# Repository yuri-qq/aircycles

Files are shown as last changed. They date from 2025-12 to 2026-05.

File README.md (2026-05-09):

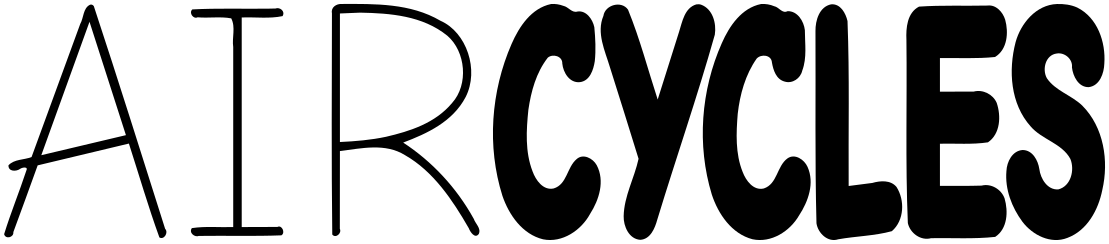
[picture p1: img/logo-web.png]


# Air Cycles

Air Cycles is our budget air purifier design for 39C3 (slogan "Power Cycles").

It is a [Corsi-Rosenthal box][cr] heavily inspired by the "Luggable" design by [cleanairkits][] (5 fans version).

<table><tr>
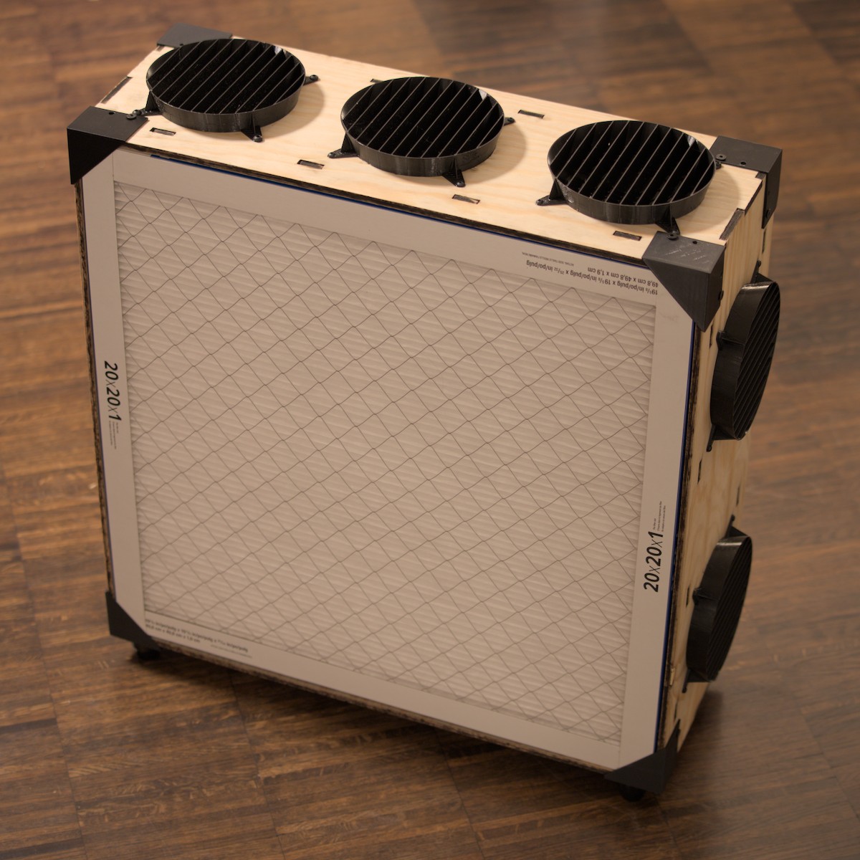
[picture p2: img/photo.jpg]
Photo of a fully assembled unit
   <td></td>
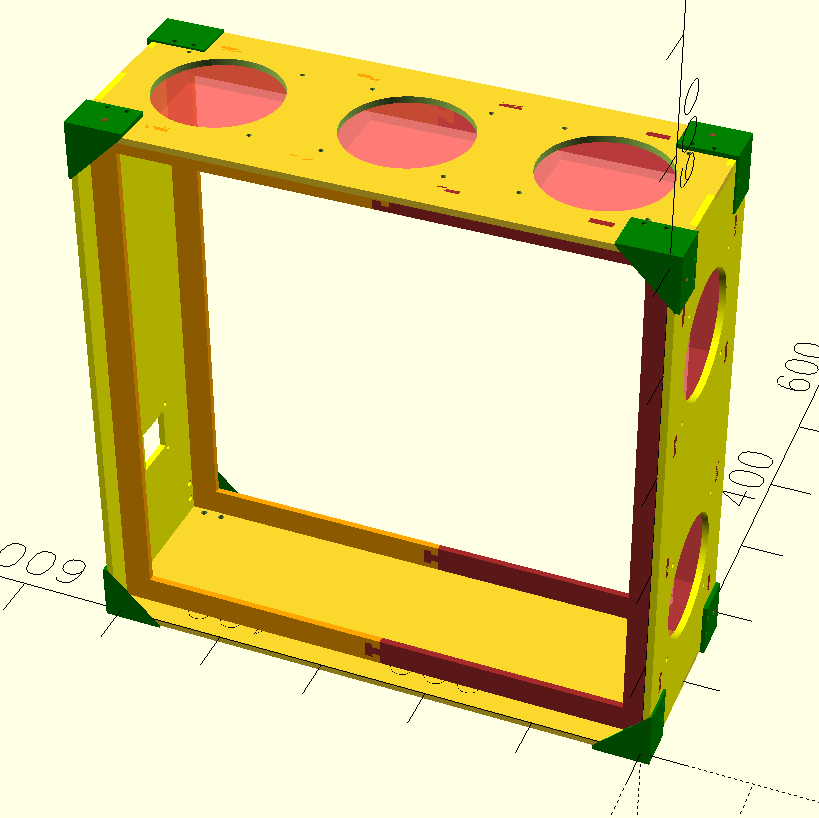
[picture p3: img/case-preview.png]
Preview 3D render in openscad
   <td></td>
</tr></table>

[cr]: https://en.wikipedia.org/wiki/Corsi%E2%80%93Rosenthal_Box
[cleanairkits]: https://www.cleanairkits.com

## Goals

* Filter airborne viruses from the air
* Use filters with the least air resistance
* Quiet enough to not be a nuisance
* Reasonably cheap
* Easy to assemble and disassemble
* Compact for storage
* Parametric design, adaptable to any filter size
* Look moderately professional

## Why?

We're the infektionsschutz team of 39C3. We take care of buying and distributing masks and tests.

This year we tried and failed to get some budget (money and storage) allocated for air purifiers. So we decided to make our own with a focus on being able to store them ourselves between events.

Also, for fun, to learn to work with wood, to use the laser cutter at the local makerspace.

## Is it any good?

For air filtering, we expect it to perform at least as well as the cleanairkits [Luggables "5 SickleFlow DIY KIT"](https://www.cleanairkits.com/en-eu/products/luggables-europe?variant=51819663655212). Their website has plenty of information about efficiency.

We don't have any budget to do real testing ourselves, but we can do a rough estimation of Dust/Virus CADR by multiplying the sum of CFM of all fans by 0.7. This ignores several variables, like pressure specs of the fans and size of the filters, but hopefully errs on the conservative side.

| Cleanairkits designs | Raw CFM | Dust CADR (measured)  |
| --- | --- | --- |
| 5 Sickleflow (16x25x1") | 310 | 218 |
| 7 Sickleflow (20x25x1") | 434 | 323 |
| 7 Mobius 120p (20x25x1") | 526 | 401 |

All our variants use 20x20x1" filters, equivalent to the 16x25x1" ones. Almost all of them have 5 fans, but except the last one in this list which has 6 as an experiment.

| Variants we've used in v1 | Raw CFM | Dust CADR (estimated) |
| --- | --- | --- |
| 5 Mobius 120 | 316 | 221 |
| 5 Mobius 120 OC | 441 | 308 |
| 3 Mobius, 2 Mobius OC | 366 | 256 |
| 2 Mobius, 2 Mobius OC, 1 Sunon | 441 | 309 |
| 2 Mobius, 3 Mobius OC, 1 Sunon | 530 | 371 |

In the current iteration, it is not necessarily cheaper or easier to build. Our project is more focused on ease of disassembly, reassembly, and storage.

## Decisions made for v1 (2025, 39c3)

Feel free to contact us with opinions or criticism!

### Overall shape

Two filters on a wooden frame with 5 fans on the sides pulling air inwards.

The traditional corsi-rosenthal cube takes up too much floor space, and box fans are not widely available in europe.

### Filters

Two 3M Filtrete MERV 13 / MPR 1900 filters, 20x20x1 inch.

They are the most common choice for Corsi-Rosenthal boxes and we had 10 of these in storage from previous years.

The 20x20x1 inch variant has the same surface as the 16x25x1 inch filters used by cleanairkits in their 5 fan Luggable model.

These filters are typically easily acquirable in europe through digikey, although the 20x20x1 inch variant has been out of stock for a few months.

**Next year:** we'll evaluate european sources for filters, likely F7 ePM1.

### Fans

A mix of five of these 120mm fans:

* Coolermaster Mobius 120
* Coolermaster Mobius 120 OC
* Sunon EEC0381B1-000U-A99

Typically three Mobius 120 OC and two Mobius 120.

Primarily inspired by cleanairkits, these fans have a great balance of static pressure specs and noise levels.

The Mobius 120 OC variant is slighly noisier but has significantly better static pressure, and happened to be cheaper at times.

In some cases where noise is more tolerated, we added some Sunon fans (EEC0381B1-000U-A99) to the mix, which have excellent static pressure specs, better airflow, more professional datasheets, but are completely uninterested in being quiet.

**Considered but rejected:** Everyone loves Noctua but most of their fans focus on airflow, not static pressure, so they are not suitable for putting a filter in front of them. Only their newest model, "NF-A12x25 G2 PWM", has slightly better pressure than the Mobius 120 at the same noise level and airflow, but for three times the price.

**Next year:** possibly more Sunon fans in the mix, as we found some locations are very tolerant of noise.

### Laser cut frame

This is the most experimental part.

4mm or 6mm plywood, pine.

The design itself is more complex than the cleanairkits one, with the structure being provided by an inner wooden frame and 3D printed parts instead of tensioners.

Plywood was recommended to us for this project by a fellow member of the makerspace, since MDF is porous which makes it not suitable for our project. Unfortunately plywood has the tendency to warp, and this makes the process of laser cutting a lot more involved.

Our first two production units were made out of 4mm sheets, which took about 10 minutes of laser time each, but with significant manual intervention.

Our next three production units were made out of 6mm sheets, which were flattened ahead of time, but laser time increased to 60 minutes and the edges were very burnt, so they required about three hours of sanding by hand afterwards.

The 6mm variant is a lot more sturdy but it's not clear it's worth the effort.

**Next year:** More material experimentation. Probably MDF with a coating.

### 3D printed parts

Corner pieces provide extra structural integrity.

Fan shrouds that are raised outwards slightly improve airflow/noise and finger-proof the fans.

### Logo font

Comic Neue.

The Kario font used by 39c3 is non-free and the author did not reply to our request to use it for this project (which extends beyond 39c3)

## Assembly instructions

This is a draft, we don't necessarily recommend building one, but please reach out to us if you actually want to.

### Parts required

* Fans
    * Coolermaster Mobius 120 or Mobius 120 OC
* Filters
    * Any MERV 13 or F7 ePM1 filter
    * Size is a parameter
    * v1 uses 3M filtrete 20x20x1" MERV 13 (Actual measures 49.8 x 49.8 x 1.9 cm)
* Wood
    * Thickness is a parameter
    * v1 uses 4mm or 6mm plywood, at least 121 x 53 cm or two squares of 60 x 53 cm, but leave some margin for magnets
* M4 Screws, 12mm and 20mm
    * It might make sense to use significantly longer ones than 20mm for the fans to simplify assembly
    * Might require accounting for material thickness
* M4 Nuts
* Barrel jack connectors
* Fan hubs
* Foam tape
* Screw inserts (for wood)
* Heat set inserts (for 3d printed parts)
* Rubber feet
* Right angle pin header
* Perfboards
* Power supply (12V, 1-3 A depending on fans)
* Wires for power (thick enough)

### Files in this repo

The openscad source files are at the root:

* `case.scad`: Outputs the laser cut box (on render) and the 3D printed corner pieces ("triangle_only" in the parameters)
* `fan-shroud.scad`: For 3D printing
* `power-mount-cylinder.scad`: For 3D printing
* `handle.scad`: For 3D printing

And these three optional parts:

* `fan-cover.scad`: For 3D printing, alternative to the shroud when one fan is missing.
* `power-mount-flat.scad`: For 3D printing, simpler version of the power mount
* `foot.scad`: For 3D printing, alternative to buying rubber feet. Preferably print with flexible filament such as TPU.

The `rendered` subdirectory contains dxf (for laser cutting) and stl (for 3D printing) files for 4mm and 6mm material thickness, all with 498x498x20mm filters and 120mm fans.

A complete unit is made of these parts:

* 1x case-?mm.dxf
* 2x corner-?mm-feet.stl
* 2x corner-?mm-feetalt.stl
* 4x corner-?mm-nofeet.stl
* 5x fan-shroud.stl (or fan-cover.stl)
* 1x power-mount-cylinder.stl or power-mount-flat.stl
* 1x handle.stl

And optionally these parts:
* 4x foot.stl

### Steps

* Buy wood
* Laser cut box out of wood
* Optionally postprocess wood (sanding, coating)
* 3D print corners, shrouds, power mount and the handle
    * The files are already in the preferred print orientation
    * 0.25mm layer height is fine
    * PETG preferred
* Install heat set inserts to corners
* Find which side of wood to put together (more preferable bend direction, less ugly side)
* Screw on the machine screw / wood screw attachment on the wood
* Put foam tape along the inner frame
* Install fans alongside the fan shroud to the pieces of wood with the fan holes
* Install the power setup
    * Fans to hub
    * Hub to perfboard with right angle pin header
    * Cables from barrel jack connector to perfboard
* Start to close up the box by putting pieces together
* Install one half of the corners (4)
* Put in the filters
* Then install the last 4 corners
* Install the handle

### Costs

This table is incomplete, and notably does not include many parts we already had around, laser operation costs, 3D printing filament and power.

Prices are an example for building a single unit, and get slightly better in bulk.

Prices include VAT.

| Item | Quantity | Unit cost | Total |
| --- | --- | --- | --- |
| Coolermaster Mobius 120 | 5 | 14.79 EUR | 73.70 EUR |
| 3M filtrete 20x20x1" MERV 13 | 2 | 24.25 EUR | 48.50 EUR |
| Plywood, pine, 600x1200x4mm  | 1 | 12.99 EUR | 12.99 EUR |
| Power supply | 1 | 10.00 EUR | 10.00 EUR |
| **Total** | | | **145.19 EUR** |

## Donations

As mentioned above, we did this whole project with no budget from congress orga, so we spent about 700 EUR from our own pockets to build the first five units. We would love to build a lot more than five units next year.

You can donate to us through these links:

* https://bunq.me/aveao
* https://paypal.me/aveaoz

Please use transfer reference "Aircycles Donation" or "Aircycles Spende". The first link also has an IBAN for direct bank transfers.

We don't intend to make a profit, so if we happen to get too many donations we'll temporarily remove the link.

## Contact

You can open issues on this repo or email us at:

* aircycles@ave.zone
* dequis\@dequis.org

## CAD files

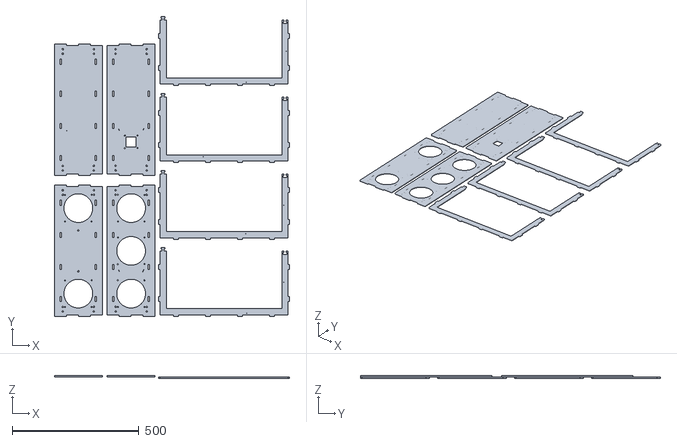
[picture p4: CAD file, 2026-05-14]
rendered/case-6mm.stl
926.8 x 1181.5 x 12.0

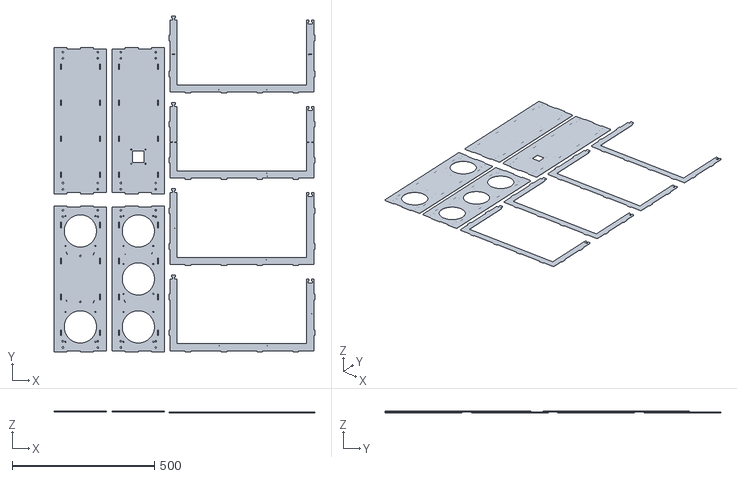
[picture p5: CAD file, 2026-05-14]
rendered/case-4mm.stl
916.0 x 1179.5 x 8.00

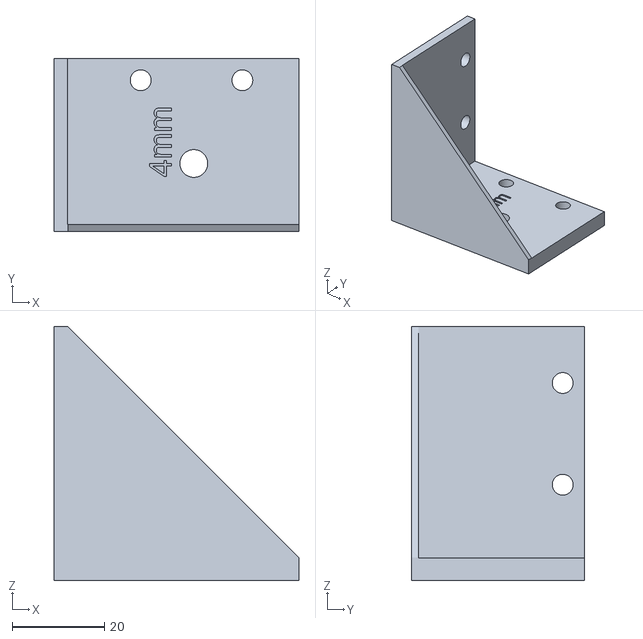
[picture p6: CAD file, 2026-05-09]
rendered/corner-4mm-feet.stl
53.0 x 37.5 x 55.0

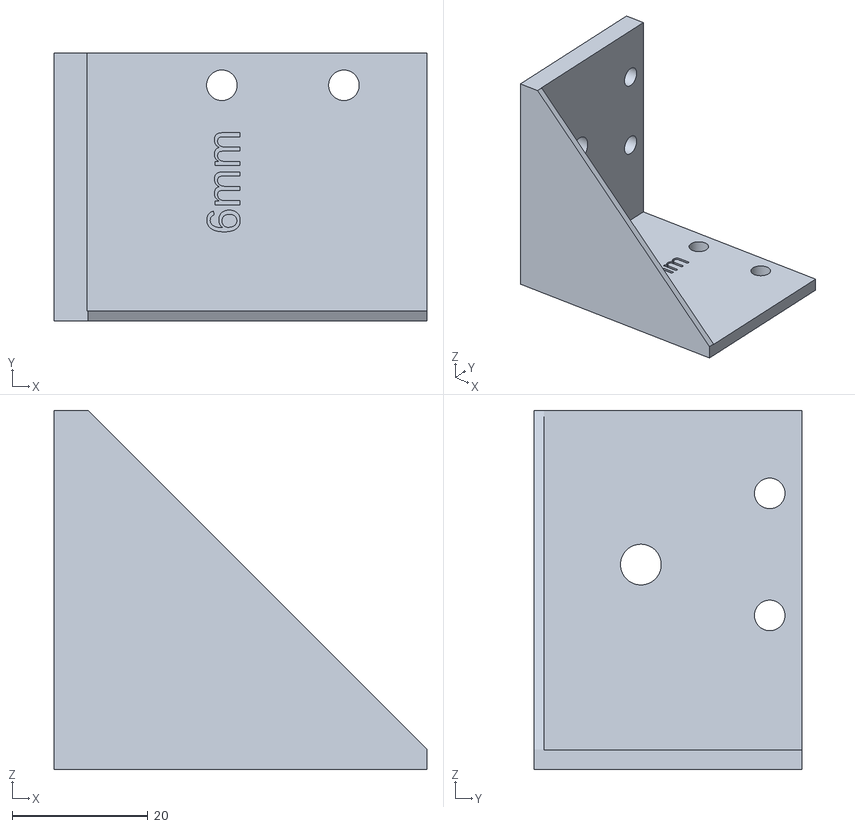
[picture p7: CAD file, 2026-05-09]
rendered/corner-6mm-feetalt.stl
55.0 x 39.5 x 53.0

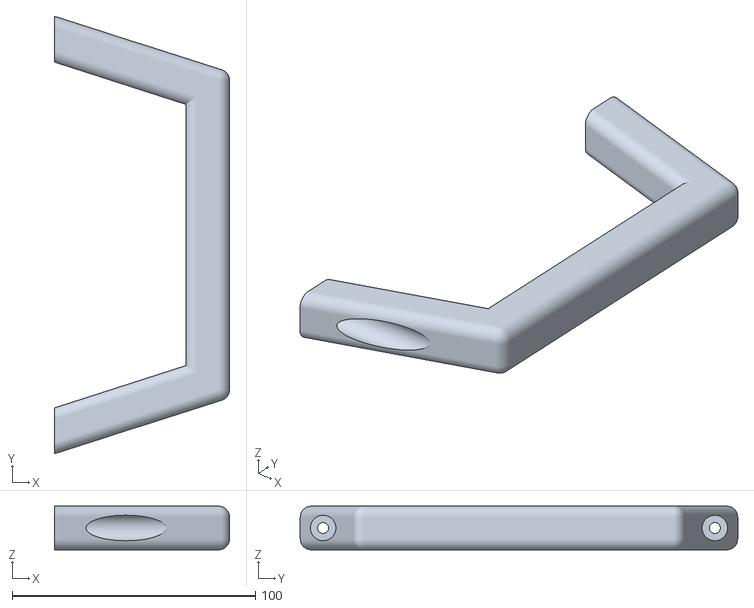
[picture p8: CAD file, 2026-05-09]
rendered/handle.stl
72.0 x 180.0 x 18.0

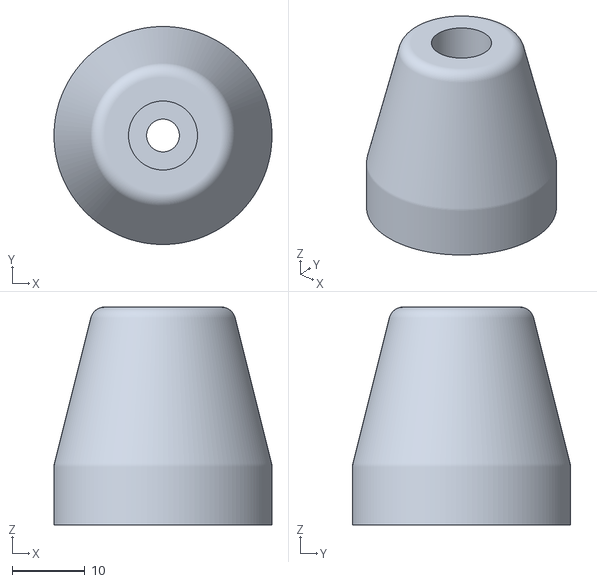
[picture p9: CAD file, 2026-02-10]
rendered/foot.stl
30.0 x 30.0 x 30.0

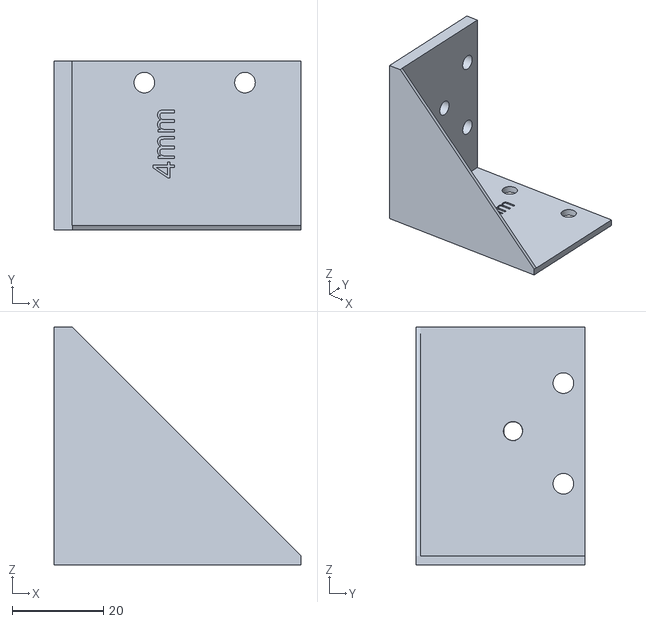
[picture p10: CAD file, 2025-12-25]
rendered/corner-4mm-nofeet.stl
54.0 x 37.0 x 52.0

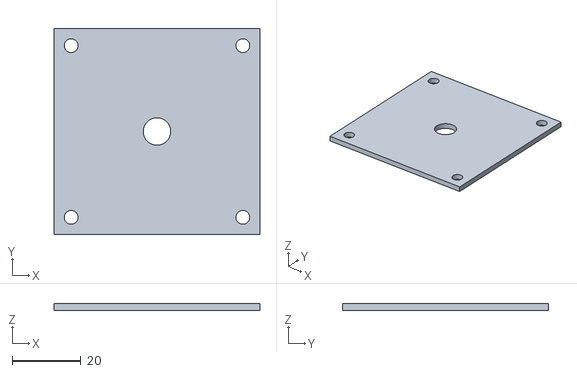
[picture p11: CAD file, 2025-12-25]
rendered/power-mount-flat.stl
60.0 x 60.0 x 1.95

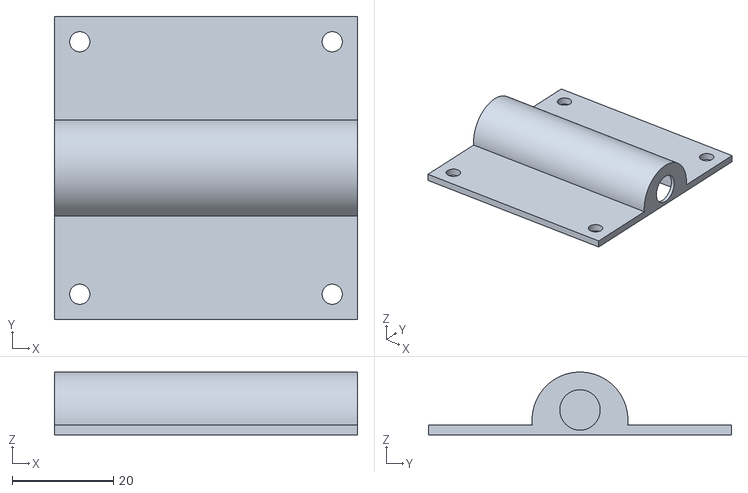
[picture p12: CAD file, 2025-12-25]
rendered/power-mount-cylinder.stl
60.0 x 60.0 x 12.4

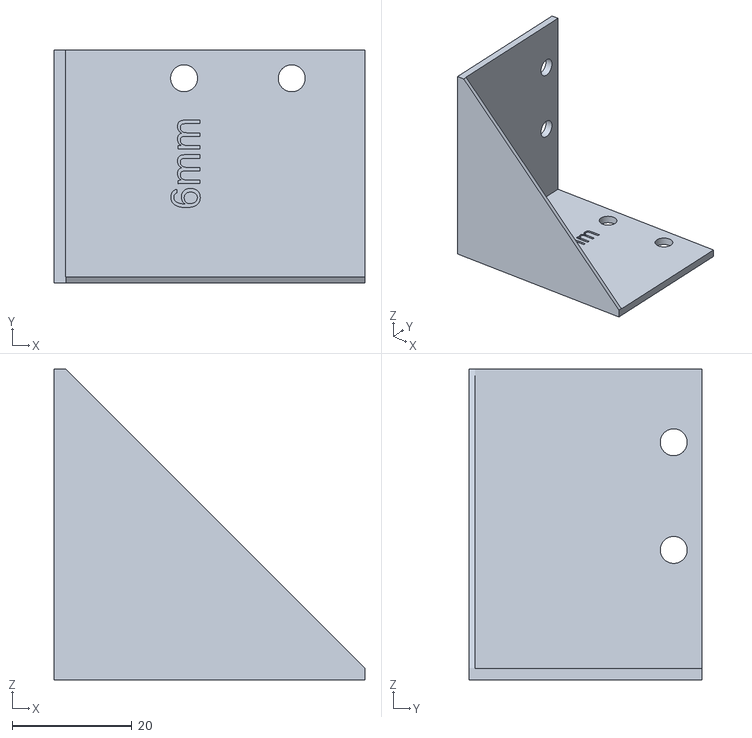
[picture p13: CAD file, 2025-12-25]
rendered/corner-6mm-nofeet.stl
52.0 x 39.0 x 52.0

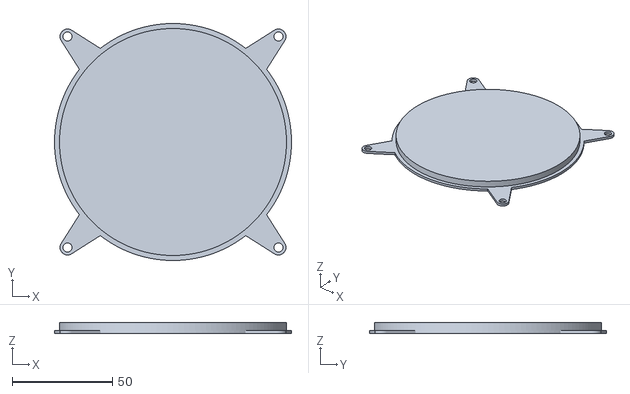
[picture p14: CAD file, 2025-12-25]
rendered/fan-cover.stl
118.0 x 118.0 x 5.50

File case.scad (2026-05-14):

$fn=128;

use <fan-shroud.scad>
use <handle.scad>
use <power-mount-cylinder.scad>

filter_width = 498+2+5;
filter_height = 498+2+5;
filter_depth = 20+2;
material_thickness = 6;

fan_dia = 120 - 7; // 7mm less so we don't expose edges too much
screw_hole_distance = 105;
screw_hole_dia = 4.5;
corner_screw_hole_dia = 6;
triangle_screw_hole_dia = screw_hole_dia;

middle_area_space = fan_dia + 20; // random number

overall_depth = filter_depth * 2 + material_thickness * 2 + middle_area_space;

primary_fans_count = 3;
secondary_fans_count = 2;

corner_teeth_count = 4;

debug_fan_dia = fan_dia;
debug_fan_height = 26.6;

middle_piece_border_size = 25; // measures 27mm
middle_piece_teeth_size = 20;
middle_piece_teeth_count = 4;  // must be an even number

corner_tri_size = 50;
corner_tri_thickness = 3;
screw_hole_side_offsets = [10+material_thickness, corner_tri_size-10-material_thickness];
screw_hole_inward_offset = filter_depth + material_thickness + 3;

echo(overall_depth);

triangle_only = false;
draw_triangle_with_feet_holes = true;
draw_triangle_with_alt_holes = true;

draw_handle_screw_holes = true;
handle_screw_hole_dia = 4.5;
handle_washer_hole_dia = 10.5;
handle_length = 180;
handle_height = 65;
handle_thickness = 18;
handle_angle = 17;

render_for_3d_printing = false;
filter_side_joint_count = 2;
filter_side_joint_depth = 10;
filter_side_joint_inner_width = 90;
filter_side_joint_outer_width = 100;
middle_fit_height_joint_count = 2;
middle_fit_width_joint_count = 1;
middle_fit_joint_depth = 6;
middle_fit_joint_inner_width = 8;
middle_fit_joint_outer_width = 12;

preview_fan_shrouds = false;
preview_handle = true;
preview_power_mount = true;

// TODO: something for power port

module draw_teeth(even=true) {
    for (i = [0:corner_teeth_count-0.01]) {
        if ((even == true && i % 2 == 0) || (even == false && i % 2 == 1)) {
            translate([i * overall_depth / corner_teeth_count, 0]) cube([overall_depth / corner_teeth_count, material_thickness, material_thickness]);
        }
    }
}

module draw_dovetail_joint(length, depth, inner_width, outer_width, tolerance=0.2) {  
    // calculate offset to keep tolerance at the corners
    dovetail_offset = tolerance / (depth / sqrt(pow(outer_width - inner_width, 2) + pow(depth, 2)));
    
    #linear_extrude(material_thickness) polygon(points=[
                [0, 0],
                [0, tolerance],
                [length/2-inner_width/2, tolerance],
                [length/2-outer_width/2, depth],
                [length/2+outer_width/2, depth],
                [length/2+inner_width/2, tolerance],
                [length, tolerance],
                [length, 0],
    
                [length/2+inner_width/2-dovetail_offset, 0],
                [length/2+outer_width/2-dovetail_offset, depth-tolerance],
                [length/2-outer_width/2+dovetail_offset, depth-tolerance],
                [length/2-inner_width/2+dovetail_offset, 0],
                [0, 0],
            ]);
}

module draw_outer_side(length, teeth_even=true) {
    difference () {
        union() {
            // TODO: length may need to slightly be increased to accommodate parts fitting together neatly
            cube([overall_depth, length, material_thickness]);
            translate([0, -material_thickness]) draw_teeth(even=teeth_even);
            translate([0, length]) draw_teeth(even=teeth_even);
        }

        for (side_alt = [0:1]) {
        // middle piece teeth
        for (i = [0:middle_piece_teeth_count-1]) {
            side_offset_by = side_alt ? overall_depth - filter_depth - material_thickness : filter_depth;
            horiz_offset_by = length/8 + ((length/4) * i);

            translate([side_offset_by, horiz_offset_by - (middle_piece_teeth_size/2), -0.5]) cube([material_thickness, middle_piece_teeth_size, material_thickness + 1]);
        }

        for (horiz_alt = [0:1]) {
        for (hole_side_offset = screw_hole_side_offsets) {
            hole_overall_inward_offset = horiz_alt ? screw_hole_inward_offset + (screw_hole_dia/2) : overall_depth - screw_hole_inward_offset - (screw_hole_dia/2);
            hole_overall_side_offset = side_alt ? hole_side_offset - (screw_hole_dia/2) : length - hole_side_offset + (screw_hole_dia/2) ;
            translate([hole_overall_inward_offset, hole_overall_side_offset, -5]) cylinder(h=material_thickness+10, d=corner_screw_hole_dia);
            }
        }
        }
        
        if(render_for_3d_printing && !$preview) {
            for(i=[1:1:filter_side_joint_count]) {
                #translate([0, i*(length/(filter_side_joint_count+1)), 0]) draw_dovetail_joint(overall_depth, filter_side_joint_depth, filter_side_joint_inner_width, filter_side_joint_outer_width);
            }
        }
    }
}

module draw_power_mount() {
    power_height = 40;
    power_width = 40;
    power_screw_distance = 50;
    translate([power_height/-2, power_width/-2, -0.05]) cube([power_height, power_width,material_thickness+0.1]);
    for (rot =[0:90:360]) {
        rotate([0, 0, rot]) translate([power_screw_distance/2, power_screw_distance/2, -0.05]) cylinder(h=material_thickness+0.1, d=screw_hole_dia);
    }
}

module draw_fan_mount() {
    translate([0, 0, -0.05]) cylinder(h=material_thickness+0.1, d=fan_dia);
    for (rot =[0:90:360]) {
        rotate([0, 0, rot]) translate([screw_hole_distance/2, screw_hole_distance/2, -0.05]) cylinder(h=material_thickness+0.1, d=screw_hole_dia);
    }
    #translate([-debug_fan_dia/2, -debug_fan_dia/2, -debug_fan_height]) cube([debug_fan_dia, debug_fan_dia, debug_fan_height]);
}

module draw_fan_side(fan_count, length, teeth_even=true, handle=false) {
    assert(!handle || fan_count % 2 == 0, "Handle can only be added with an even number of fans!");

    loop_count = handle ? fan_count + 1 : fan_count;

    // fan_gap = (filter_width % fan_dia) / floor(filter_width / fan_dia);
    fan_gap = (length - (loop_count * fan_dia)) / loop_count;

    difference() {
        draw_outer_side(length=length, teeth_even=teeth_even);

        translate([0, fan_gap/2, 0]) for (i = [0:1:loop_count-1]) {
            offset_by = fan_dia/2 + (fan_dia + fan_gap) * i;
            if(handle==false || i != floor(loop_count / 2)) {
                translate([overall_depth/2, offset_by, 0]) draw_fan_mount();
            }
        }
        
        if(handle) draw_handle_screw_holes(handle_length, handle_height, handle_thickness, handle_angle);
    }
    
    if($preview) {
        if(handle && preview_handle) {
            translate([overall_depth/2+handle_thickness/2, filter_width/2-handle_length/2, material_thickness])  draw_handle(handle_length, handle_height, handle_thickness, handle_angle, handle_screw_hole_dia, handle_washer_hole_dia);
        }
    
        if(preview_fan_shrouds) {
            translate([0, fan_gap/2, 0]) for (i = [0:1:loop_count-1]) {
                offset_by = fan_dia/2 + (fan_dia + fan_gap) * i;
                if(handle==false || i != floor(loop_count / 2)) {
                    translate([overall_depth/2, offset_by, material_thickness]) rotate([0,0,90]) draw_fan_shroud();
                }
            }
        }
    }
}

module draw_power_side(length, teeth_even=true) {
    difference() {
        draw_outer_side(length=length, teeth_even=teeth_even);
        translate([overall_depth/2, length/4, 0]) draw_power_mount();
    }
    
    if($preview && preview_power_mount) translate([overall_depth/2, length/4, 0]) rotate([0,180,90]) draw_power_mount_cylinder();
}

module draw_middle_fit_old() {
    difference() {
        cube([material_thickness, filter_width, filter_height]);
        translate([-0.05, middle_piece_border_size, middle_piece_border_size]) cube([material_thickness+0.1, filter_width - middle_piece_border_size*2, filter_height - middle_piece_border_size*2]);
    }
}

module draw_middle_fit_hole(flip=false) {
    width = flip ? filter_width : filter_height;
    height = flip ? filter_height : filter_width;

    for (i = [0:middle_piece_teeth_count-1]) {
        offset_by = width/8 + ((width/4) * i);
        rotate([90, 0, 90]) linear_extrude(material_thickness) polygon(points=[
                [0, 0],
                [0, offset_by - (middle_piece_teeth_size/2)],
                [-material_thickness, offset_by - (middle_piece_teeth_size/2)],
                [-material_thickness, offset_by + (middle_piece_teeth_size/2)],
                [0, offset_by + (middle_piece_teeth_size/2)],
            ]);
    }
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

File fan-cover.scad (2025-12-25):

$fn=128;


fan_dia = 120 - 7; // 7mm less so we don't expose edges too much
screw_hole_distance = 105;
screw_hole_dia = 4.5;
material_thickness = 1.5;

fan_count = 3;

side_length = 498+2+5;

extra_border = 5;
in_between_gap = 0.5;

shroud_height = material_thickness;

module draw_circle_outlines(dia, height, thickness) {
    difference() {
        cylinder(h=height, d=dia+thickness);
        translate([0, 0, -0.05]) cylinder(h=height+0.1, d=dia);
    }
}

module draw_fan_holes() {
    difference() {
    union() {
        for (alt = [0:90:359]) {
            union() {
                // screw hole attachment things
                hull() {
                    rotate([0, 0, alt]) translate([screw_hole_distance/2, screw_hole_distance/2]) cylinder(h=material_thickness, d=screw_hole_dia+3);
                    cylinder(h=material_thickness, d=40);
                }
            }
        }
    }
    union() {
        translate([0, 0, -0.05]) cylinder(h=shroud_height, d1=fan_dia);
        for (rot =[0:90:360]) {
            rotate([0, 0, rot]) translate([screw_hole_distance/2, screw_hole_distance/2, -0.05]) cylinder(h=material_thickness+10, d=screw_hole_dia);
        }
    }
    }
}

fan_gap = (side_length - (fan_count * fan_dia)) / fan_count;

intersection() {
    // shroud
    union() {
        cylinder(h=shroud_height, d=fan_dia+extra_border);
        cylinder(h=shroud_height+4, d=fan_dia);
        // bottom part
        draw_fan_holes();
    }
}

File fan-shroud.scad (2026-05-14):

$fn=128;


fan_dia = 120 - 7; // 7mm less so we don't expose edges too much
shroud_upper_dia = 125;
screw_hole_distance = 105;
screw_hole_dia = 4.5;
material_thickness = 1.5;

fan_count = 3;

side_length = 498+2+5;

extra_border = 5;
overall_depth = shroud_upper_dia + extra_border;
in_between_gap = 0.5;

shroud_thickness = 1;
shroud_gap = 10;
shroud_height = 20;
shroud_angle = 3;

center_circle_dia = 30;

finger_protection_gap = 11;
finger_protection_thickness = 1.5;

screw_protection_thickness = 1;

// middle circle to cover fan brand -> done
// finger protection -> done
// 1mm extra to the holes sides -> done
// extra protection on the screw holes -> done
// center grills -> done

module draw_circle_outlines(dia, height, thickness) {
    difference() {
        cylinder(h=height, d=dia+thickness);
        translate([0, 0, -0.05]) cylinder(h=height+0.1, d=dia);
    }
}

module draw_fan_holes() {
    difference() {
    union() {
        for (alt = [0:90:359]) {
            union() {
                // screw hole attachment things
                hull() {
                    rotate([0, 0, alt]) translate([screw_hole_distance/2, screw_hole_distance/2]) cylinder(h=material_thickness, d=screw_hole_dia+3);
                    cylinder(h=material_thickness+5, d=40);
                }
                // screw hole attachment protection
                hull() {
                    rotate([0, 0, alt]) translate([screw_hole_distance/2, screw_hole_distance/2, - screw_hole_dia - screw_protection_thickness - 15]) cylinder(h=material_thickness, d=screw_protection_thickness);
                    rotate([0, 0, alt-45]) translate([0, (shroud_upper_dia+(material_thickness/2))/2, shroud_height]) cylinder(h=0.01, d=screw_protection_thickness);
                    rotate([0, 0, alt-45]) translate([0, (fan_dia+(material_thickness/2))/2, 0]) cylinder(h=0.01, d=screw_protection_thickness);
                }
            }
        }
    }
    union() {
        translate([0, 0, -0.05]) cylinder(h=shroud_height, d1=fan_dia+material_thickness, d2=shroud_upper_dia+material_thickness);
        for (rot =[0:90:360]) {
            rotate([0, 0, rot]) translate([screw_hole_distance/2, screw_hole_distance/2, -0.05]) cylinder(h=material_thickness+10, d=screw_hole_dia);
        }
    }
    }
}

module draw_cylinder_around_fan() {
    difference() {
        cylinder(h=shroud_height, d1=fan_dia+material_thickness, d2=shroud_upper_dia+material_thickness);
        translate([0, 0, -0.5]) cylinder(h=shroud_height+1, d1=fan_dia, d2=shroud_upper_dia);
    }
}

module draw_fan_shroud() {
    fan_gap = (side_length - (fan_count * fan_dia)) / fan_count;

    intersection() {
        // cutting off sides
        translate([overall_depth/-2, (shroud_upper_dia+extra_border)/-2, 0]) cube([overall_depth, shroud_upper_dia + (extra_border*2), material_thickness + shroud_height]);

        // shroud
        union() {
        // cylinder around fan
        draw_cylinder_around_fan();

        intersection() {
            offset_shroud_overall_by = overall_depth % (shroud_thickness+shroud_gap);
            cylinder(h=shroud_height, d1=fan_dia+material_thickness, d2=shroud_upper_dia+material_thickness);
            for (shroud_offset = [offset_shroud_overall_by:shroud_thickness+shroud_gap:overall_depth]) {
                translate([overall_depth/-2 +shroud_offset, (fan_dia + fan_gap - in_between_gap)/-2, 0]) rotate([0, shroud_angle, 0]) cube([shroud_thickness, fan_dia + fan_gap - in_between_gap, shroud_height + 5]);
            }
        }
        // middle circle for fan logo
        cylinder(h=material_thickness, d=center_circle_dia);
        // finger protection
        for (finger_protection_dia = [center_circle_dia:finger_protection_thickness+finger_protection_gap:fan_dia]) {
            draw_circle_outlines(dia=finger_protection_dia, height=material_thickness, thickness=finger_protection_thickness);
        }
        // finger protection strengthening
        intersection() {
            translate([shroud_upper_dia/-2, finger_protection_thickness/-2, 0]) cube([shroud_upper_dia, finger_protection_thickness, material_thickness]);
            cylinder(h=shroud_height, d1=fan_dia, d2=shroud_upper_dia);
        }
        // bottom part
        draw_fan_holes();
        }
    }
}

draw_fan_shroud();

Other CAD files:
rendered/corner-6mm-feet.stl
rendered/corner-4mm-feetalt.stl
foot.scad
handle.scad
power-mount-cylinder.scad
power-mount-flat.scad
rendered/case-4mm.dxf
rendered/case-6mm.dxf

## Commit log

2025-12-25 add case-preview.png
2025-12-25 Add source openscad and rendered dxf/stl files
    [case-4mm.dxf, case-6mm.dxf, case.scad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]
2026-02-06 Fix corner triangles for thicknesses greater than 2mm
    This fixes small issues with the corner triangle hull and feet screw holes at thicknesses greater than 2.
    Also sets the right parameters for them in the preview.
    [case.scad]
2026-02-10 Add 3D printable feet design
    These can be used as an alternative to buying rubber feet
    [foot.scad, foot.stl]
2026-05-09 Add carrying handle to the design
    Without a handle it can get a little awkward carrying the air purifier while trying to avoid touching the filters,
    so I designed this handle to conveniently carry it.
    [case-4mm.dxf, case-6mm.dxf, case.scad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]
2026-05-09 Add 2mm to the bottom of the feet corner pieces instead of doubling the thickness
    [case.scad]
2026-05-09 Increase corner piece thickness to 3mm for more stability
    [case.scad]
2026-05-09 Increase corner feet screw hole size to 6mm for M4 heat-set inserts
    [case.scad, corner-4mm-feet.stl, corner-4mm-feetalt.stl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]
2026-05-14 Add option to render case for 3D printing
    When enabled the case is split up into multiple parts to fit a 3D printer printbed.
    The parts have dovetail joints for reassembly with glue or solvents.
    [case-4mm.stl, case-6mm.stl, case.scad]
2026-05-14 Add handle, power mount and fan shrouds to preview
    I didn't enable the fan shroud preview by default, because it made the
    preview very slow, at least on my machine.
    [case.scad, fan-shroud.scad, power-mount-cylinder.scad]
